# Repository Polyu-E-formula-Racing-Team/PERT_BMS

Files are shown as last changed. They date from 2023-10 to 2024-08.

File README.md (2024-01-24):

# PERT BMS Project

This project is intended to replace the previous BMS that has poor documentation and support. The first phase of this project is to build a fully functional BMS. The BMS doesn't need to be fancy, the only requirement for phase 1 is solid running.

## Timeline

| Milestone | Time |
|---|---|
| BSU HW design done | Jan 2024 |
| BSU SW design done | Feb 2024 |
| BSU stable version | Mar 2024 |
| BMU HW design done | Mar 2024 |
| BMU SW design done | Apr 2024 |
| BMU stable version | May 2024 |
| Fully function BMS | Jun 2024 |

## BMS Structure

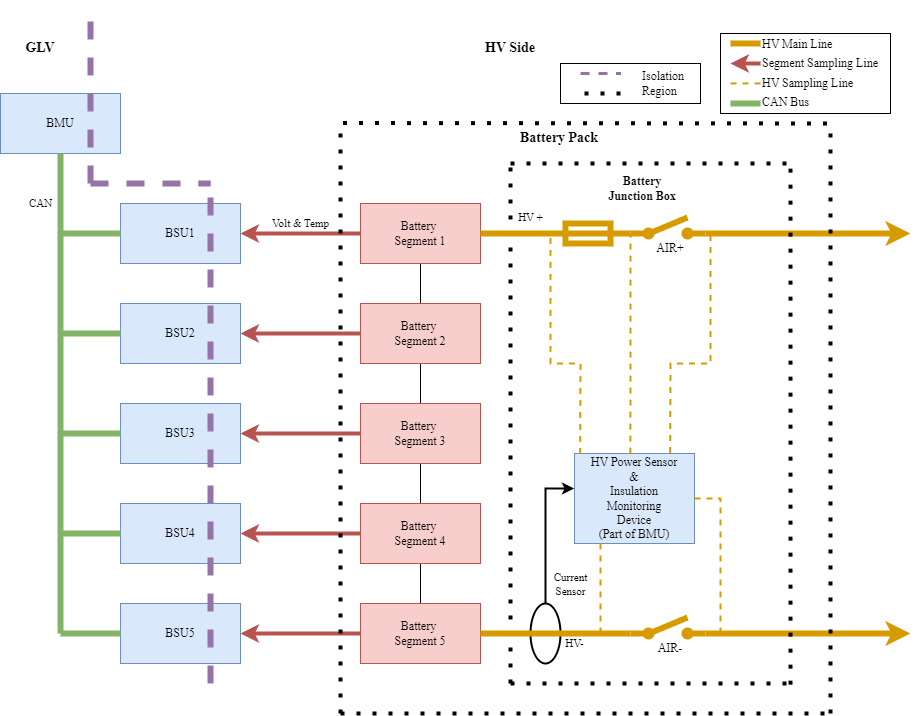
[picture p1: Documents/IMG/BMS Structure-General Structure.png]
BMS General Structure


The BMS is a distributed BMS that uses a dedicated CAN bus to share information. The core modules are 5 BSUs and 1 BMU that monitor and protect the whole accumulator.
Each BSU (Battery Sampling Unit) corresponds to one battery segment. While BMU (Battery Monitoring Unit) is monitoring the whole battery pack and coordinating the BSUs.

### BMU Structure

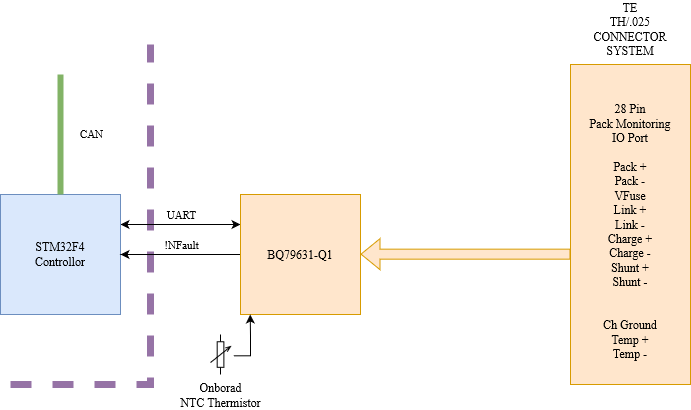
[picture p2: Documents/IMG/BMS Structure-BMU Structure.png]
BMU Structure


The BMU uses an STM32F446 MCU and a BQ76931-Q1 Battery Monitoring Chip to monitor the battery pack status. This design simplifies the design of the monitoring circuit. The core of this module is the software to estimate the SOC, SOH, DOD, etc...
The second core is the software to control cell balancing between battery packs. The third is the charging and discharge control software.

### BSU Structure

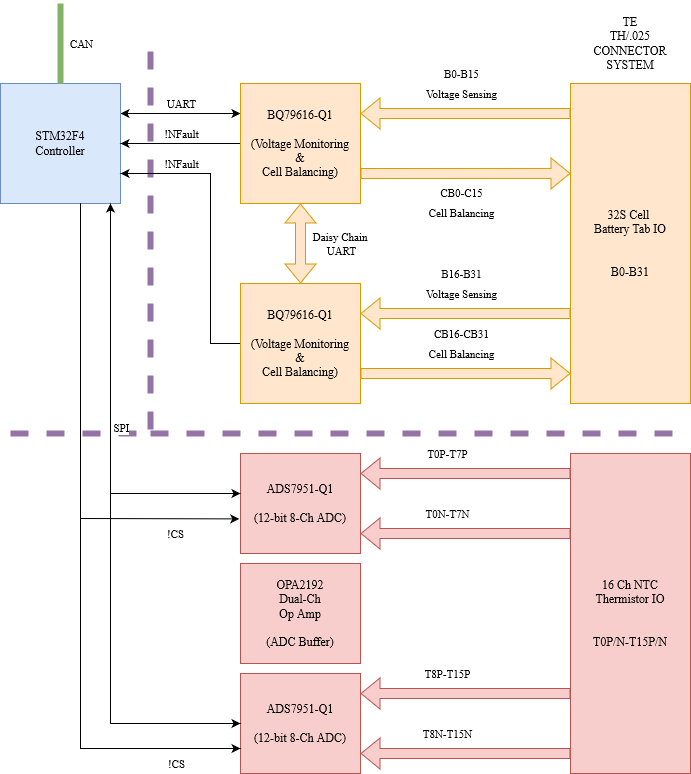
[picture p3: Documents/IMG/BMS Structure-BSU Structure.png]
BSU Structure


The BSU uses an STM32F446 MCU, two BQ79616-Q1 and two ADS7951-Q1 to sense cell property. BQ89616-Q1 measures the voltage and performs cell balancing to the battery segment.
ADS7951-Q1  sensing the temperature of the battery.
The first core of the BSU is to sample all properties and broadcast them. The second core is to control the cell balancing to quickly balance the cell voltage with the limit of 8 cells per chip.

## PCB Design

The PCBs have 4 layers of copper and use JLCPCB standard stackup. 

### BSU PCB

The BSU is 100x255 mm with 6 mounting holes. The detailed PCB design is shown in the [Description](./BSU/Documents/BSU-Description.pdf) and [Schematic](./BSU/Documents/BSU-Schematic.pdf).

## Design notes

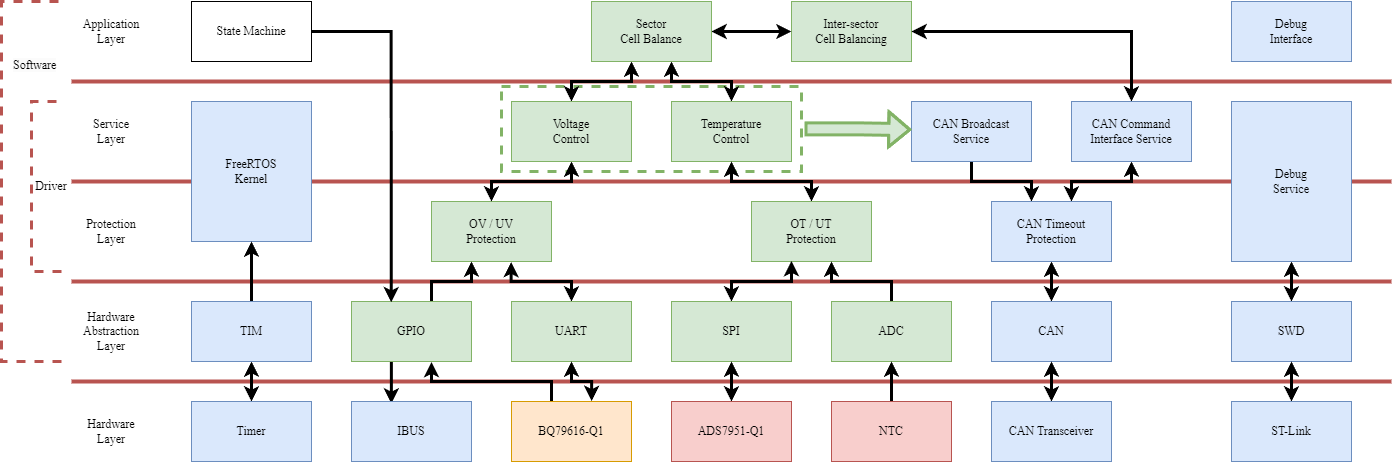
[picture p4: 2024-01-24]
Documents/IMG/BMS Structure-BSU Arch.png

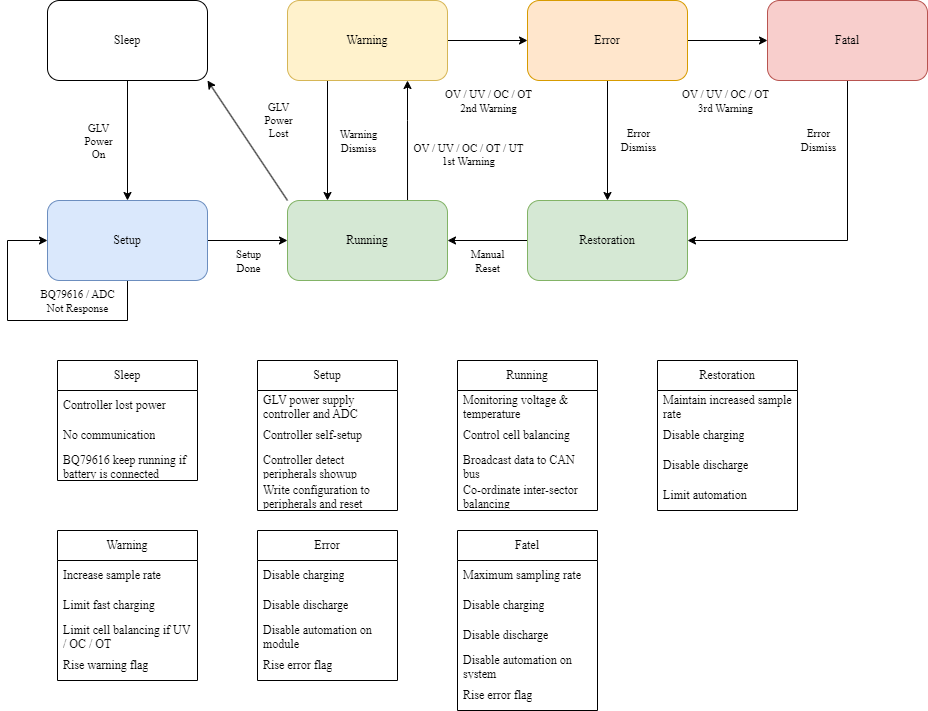
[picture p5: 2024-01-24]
Documents/IMG/BMS Structure-State Machine.png

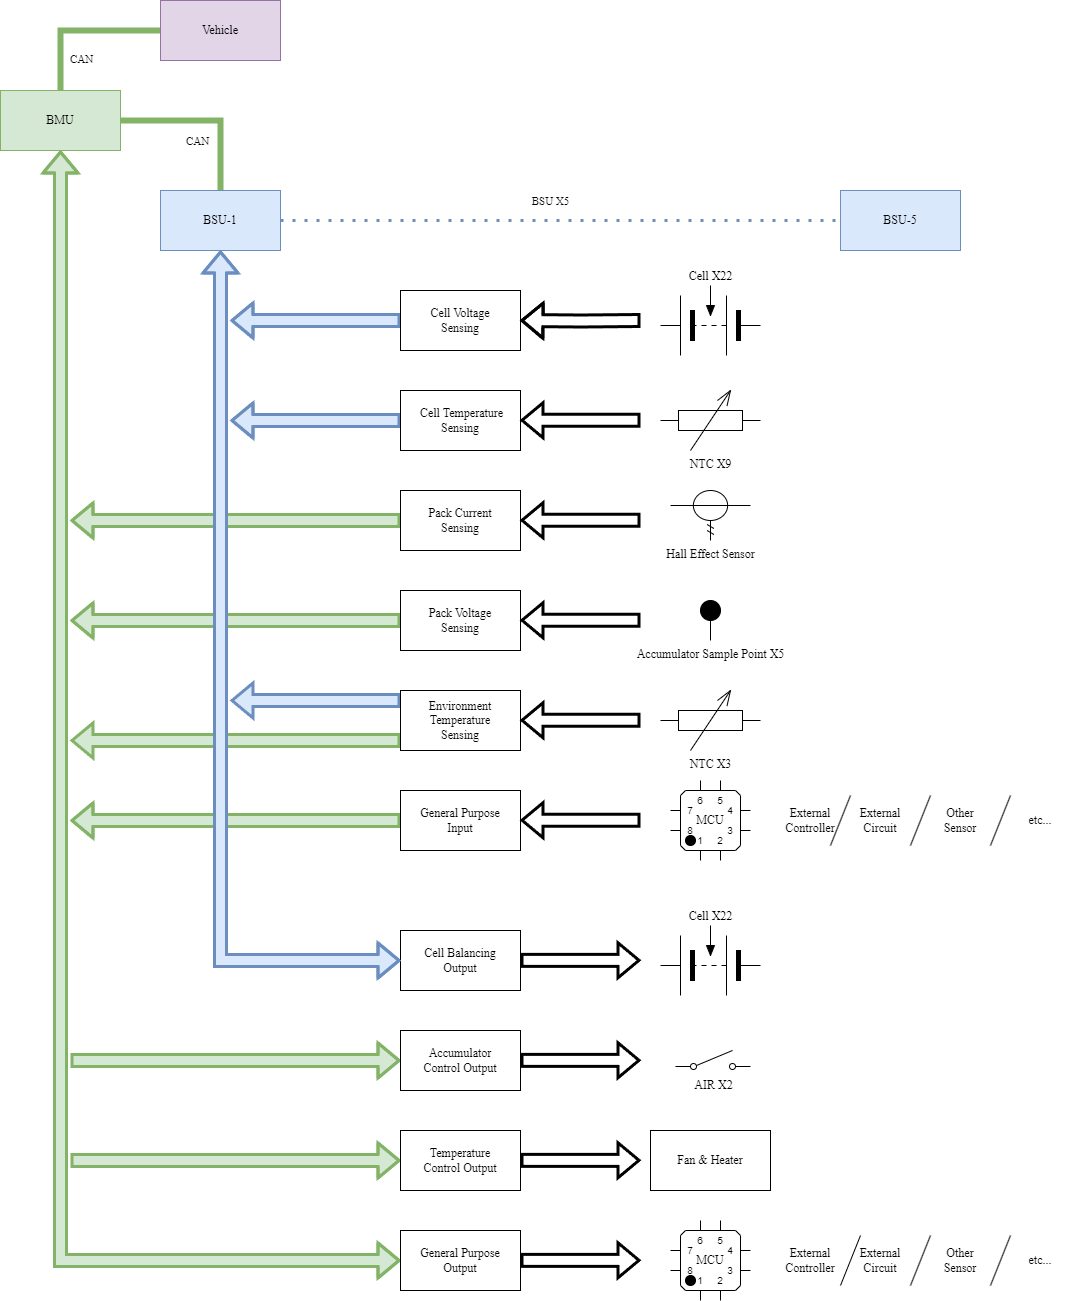
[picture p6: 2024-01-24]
Documents/IMG/BMS Structure-System IO.png

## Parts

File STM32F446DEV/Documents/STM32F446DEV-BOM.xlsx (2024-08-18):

Comment | Description | Designator | Footprint | LibRef | Quantity
NCP1117IST33T3G | Linear Voltage Regulator IC Positive Fixed 1 Output 1A SOT-223 | B1 | SOT230P700X180-4N | CMP-052-000000-1 | 1
10u | 0603 SMD Capacitor | C1, C2 | 0603_SMD_C | 0603_SMD_Capacitor | 2
100n | SMD 0603 Capacitor | C3 | 0603_SMD_RC | SMD 0603 Capacitor | 1
 | SMD 0603 Capacitor | C4, C5 | 0603_SMD_RC | SMD 0603 Capacitor | 2
Header 1x5 | Header 1x5 | J1 | HDR_1X5_2.54_SMD | Header 1x5 | 1
UJ2-MIBH-G-SMT-TR | USB Connectors USB jack, 2.0, micro B type, 5 pin, horizontal, gold flash, SMT, TR | J2 | USB_B_5P_SMD | USB_B 5P | 1
Header 1x3 | Pin Header 2.54mm Pitch STR DIP, 1x3Pin, G/F, LCP, 8.08mm*2.54mm*3.18mm, Color-Black, Bag | J3 | HDR_1X3_2.54_THD | Header 1x3 | 1
Header 1x5 | Header 2x11 | J4, J5 | HDR_2x11_2.54_THD | Header 2x11 | 2
STM32F446RET6 | No Description Available | U1 | LQFP64-STM32F446 | STM32F446RET6 | 1
ECS-1612MV-080-CN-TR | Standard Clock Oscillators 8MHz CMOS 1.6-3.6V | X1 | 1612_OSXO_80 | 8M OSXO ECS | 1
ECS-327MV-CN-TR | Standard Clock Oscillators 32.768kHz LVCMOS 1.6-3.6V | X2 | 1612_OSXO_32.768 | 32.768k OSXO ECS | 1

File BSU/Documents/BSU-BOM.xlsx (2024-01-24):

Name | Description | Designator | Footprint | Manufacturer 1 | Manufacturer_Name | Manufacturer Part Number 1 | Quantity | Supplier 1 | Supplier Currency 1 | Supplier Unit Price 1 | Supplier Subtotal 1
ADS7951QDBTRQ1 | Automotive 12 bit, 1 MSPS, 8 Channel, Single-Ended, SAR ADC | ADC1, ADC2 | TSSOP30_ADS7951 | Texas Instruments | Texas Instruments | ADS7951QDBTRQ1 | 2 | Mouser | USD | 7.42 | 14.83
BQ79616PAPR | Battery Management 16-S precision battery monitor, balancer and integrated protector with stacking interface | BQ1, BQ2 | HTQFP65_BQ79616 | Texas Instruments | Texas Instruments | BQ79616PAPRQ1 | 2 | Mouser | USD | 13.52 | 27.04
220n | 1210 SMD Capacitor | C1, C2 | 1210_SMD_C | Kyocera AVX |  | 12101C224JAT2A | 2 | Mouser | USD | 0.3903 | 0.78059
1u | 0603 SMD Capacitor | C3, C4, C13, C14, C15, C16 | 0603_SMD_C | Yageo |  | CC0603ZRY5V6BB105 | 6 | Mouser | USD | 0.03403 | 0.34026
2.2u | 0603 SMD Capacitor | C5, C6 | 0603_SMD_C | Samsung |  | CL10A225KP8NNWC | 2 | Mouser | USD | 0.10008 | 0.20015
0.1u | 0603 SMD Capacitor | C7, C8, C11, C12 | 0603_SMD_C | Yageo |  | CC0603KRX7R6BB104 | 4 | Mouser | USD | 0.04003 | 0.4003
4.7u | 0603 SMD Capacitor | C9, C10 | 0603_SMD_C | Samsung |  | CL10A475KP8NNWC | 2 | Mouser | USD | 0.10008 | 0.20015
22u | 0805 SMD Capacitor | C17, C40 | 0805_SMD_C | Murata |  | GRM21BR61C226ME44K | 2 | Mouser | USD | 0.29022 | 0.58044
1u | 0805 SMD Capacitor | C18, C20, C21, C23, C24, C33, C34, C35, C36, C37, C38, C39 | 0805_SMD_C | Samsung |  | CL21B105KBFNNNF | 12 | Mouser | USD | 0.07506 | 0.90068
10u | 0805 SMD Capacitor | C19, C22, C41, C42, C43 | 0805_SMD_C | Murata |  | GRM21BR61H106KE43L | 5 | Mouser | USD | 0.15812 | 1.58
100n | 0805 SMD Capacitor | C25, C26, C27, C28, C29, C30, C31, C32 | 0805_SMD_C | KEMET |  | C0805C104Z4VACTU | 8 | Mouser | USD | 0.04203 | 0.42032
150p | 0805 SMD Capacitor | C44, C45, C62, C63, C64 | 0805_SMD_C | KEMET |  | C0805C151J5GACTU | 5 | Mouser | USD | 0.03403 | 0.34026
150p | 0603 SMD Capacitor | C46, C47, C48, C49, C50, C51, C52, C53, C54, C55, C56, C57, C58, C59, C60, C61 | 0603_SMD_C | KEMET |  | C0603C151M5HACTU | 16 | Mouser | USD | 0.02102 | 0.33625
470n | 0603 SMD Capacitor | C65, C66, C67, C68, C69, C70, C71, C72, C73, C74, C75, C76, C77, C78, C79, C80, C81, C82, C83, C84, C85, C86, C87, C88, C89, C90, C91, C92, C93, C94, C95, C96, C97, C98, C99, C100, C101, C102, C103, C104, C105, C106, C107, C108, C109, C110, C111, C112, C113, C114, C115, C116, C117, C118, C119, C120, C121, C122, C123, C124, C125, C126, C127, C128, C129, C130 | 0603_SMD_C | Samsung |  | CL10B474KO8NFNC | 66 | Mouser | USD | 0.03102 | 2.05
470n | 0805 SMD Capacitor | C131, C132 | 0805_SMD_C | Kyocera AVX |  | 08051C474K4T2A | 2 | Mouser | USD | 0.28021 | 0.56042
10n | 0805 SMD Capacitor | C133, C134 | 0805_SMD_C | Samsung |  | CL21B103KCANNNC | 2 | Mouser | USD | 0.01901 | 0.19014
220p | 0603 SMD Capacitor | C135, C136, C141, C142 | 0603_SMD_C | Samsung |  | CL10C221JB8NFNC | 4 | Mouser | USD | 0.01801 | 0.18014
2.2n | 0603 SMD Capacitor | C137, C138, C139, C140 | 0603_SMD_C | KEMET |  | C0603C222K1RECAUTO | 4 | Mouser | USD | 0.19014 | 0.76058
824500241 | TVS Diode (Uni-directional) | D1 | SMA_824500241 | Wurth Electronics | Wurth Elektronik | 824500241 | 1 | Mouser | USD | 0.29022 | 0.29022
C1Q_1 | T&R | F1, F2, F3, F4, F5, F6, F7, F8, F9, F10, F11, F12, F13, F14, F15, F16, F17, F18, F19, F20, F21, F22, F23, F24, F25, F26, F27, F28, F29, F30, F31, F32, F33 | 1206_C1Q | Bel | Bel | C1Q1 | 33 | Mouser | USD | 0.2582 | 8.52
Header 1x2 | Header, 2-Pin | J1 | HDR_1X2_2.54_THD | Stock |  | NA | 1 | Stock | USD | 0.00128 | 0.00128
1318745-2 | TE CONNECTIVITY - 1318745-2 - Automotive Connector, TH 025 Series, Right Angle Plug, 32 Contacts, Crimp Pin | J2 | TH025_32P | Stock | TE Connectivity | NA | 1 | Stock | USD | 0.00128 | 0.00128
1318384-2 | TE Connectivity TH 025 Series, 2 Row 40 Way Through Hole Socket Automotive Header Connector, Automotive wiring | J3 | TH025_40P | Stock | TE Connectivity | NA | 1 | Stock | USD | 0.00128 | 0.00128
Header 1x3 | Pin Header 2.54mm Pitch STR DIP, 1x3Pin, G/F, LCP, 8.08mm*2.54mm*3.18mm, Color-Black, Bag | J4, J5, J10, J11, J12 | HDR_1X3_2.54_THD | Stock | Amphenol Communications Solutions | NA | 5 | Stock | USD | 0.00128 | 0.0064
Header 1x5 | Header 1x5 | J14, J15 | HDR_1X5_2.54_THD | Stock | TE Connectivity | NA | 2 | Stock | USD | 0.00128 | 0.00256
TLV75533PDBVR | LDO Voltage Regulators 500-mA, Low IQ, Small Size, Low Dropout Regulator 5-SOT-23 -40 to 125 | LDO1, LDO2 | SOT23-5_TLV75533 | Texas Instruments | Texas Instruments | TLV75533PDBVR | 2 | Mouser | USD | 0.3903 | 0.78059
RED | SMD LED | LED1, LED2, LED3, LED4, LED6 | 0805_SMD_LED | Wurth Electronics |  | 150080SS75000 | 5 | Mouser | USD | 0.19014 | 0.95072
GREEN | SMD LED | LED5 | 0805_SMD_LED | Wurth Electronics |  | 150080GS75000 | 1 | Mouser | USD | 0.19014 | 0.19014
NTCS0805E3104JXT | NTC Thermistors 100Kohms 5% SMD | NTC1, NTC2, NTC3 | 0805_SMD_R | Vishay BCcomponents | Vishay | NTCS0805E3104JXT | 3 | Mouser | USD | 0.44033 | 1.32
OPA2192IDGKT | 36-V, Precision, RRIO, Low Offset Voltage, Low Input Bias Current Op Amp With e-trim | OPA1 | VSSOP8_OPA2192 | Texas Instruments | Texas Instruments | OPA2192IDGKT | 1 | Mouser | USD | 5.44 | 5.44
VXO7805-1000 | CUI Inc.,1 A Output Current, 6~36 Vdc Input, 3 Pin SIP, Non-Isolated, Dc-Dc Converter | PS1 | VXO78xx-1000 | Stock |  | NA | 1 | Stock | USD | 0.00128 | 0.00128
PDSE1-S24-S5-M | CUI Inc., DC-DC ISOLATED, 5VDC input, 1 W, 4.5-5.5 VDC | PS2 | PDSE1-Sxx-Sx-M | Stock |  | NA | 1 | Stock | USD | 0.00128 | 0.00128
ZXTN4004KTC | Transistor | Q1, Q2, Q3, Q4 | TO252-3_ZXTN4004K | Diodes | Diodes Incorporated | ZXTN4004KTC | 4 | Mouser | USD | 0.44033 | 1.76
200 | 2010 SMD Resistor | R1, R3 | 2010_SMD_R | Bourns |  | CR2010-JW-201ELF | 2 | Mouser | USD | 0.10008 | 0.20015
100 | 2010 SMD Resistor | R2, R4 | 2010_SMD_R | Bourns |  | CR2010-JW-101ELF | 2 | Mouser | USD | 0.18014 | 0.36027
20k | 0805 SMD Resistor | R5 | 0805_SMD_R | Yageo |  | RC0805FR-0720KL | 1 | Mouser | USD | 0.10008 | 0.10008
200 | 0805 SMD Resistor | R6, R7, R8, R9, R10 | 0805_SMD_R | Yageo |  | RC0805FR-10200KL | 5 | Mouser | USD | 0.01601 | 0.16012
100 | 0805 SMD Resistor | R11, R12 | 0805_SMD_R | Yageo |  | RC0805JR-13100RL | 2 | Mouser | USD | 0.01401 | 0.14011
100k | 0603 SMD Resistor | R13, R14, R15, R16, R17, R18, R19, R20, R21, R22, R23, R24, R25, R26, R27, R28 | 0603_SMD_R | Vishay Semiconductors |  | RCA0603100KFKEA | 16 | Mouser | USD | 0.02402 | 0.38429
100k | 0805 SMD Resistor | R29, R30, R31 | 0805_SMD_R | Yageo |  | AC0805JR-07100KL | 3 | Mouser | USD | 0.01801 | 0.18014
100 | 0603 SMD Resistor | R32, R33, R34, R35, R36, R37, R38, R39, R40, R41, R42, R43, R44, R45, R46, R47, R49, R50, R51, R52, R53, R54, R55, R56, R57, R58, R59, R60, R61, R62, R63, R64, R65 | 0603_SMD_R | Yageo |  | AC0603FR-10100RL | 33 | Mouser | USD | 0.01301 | 0.42932
0 | 1210 SMD Resistor | R48 | 1210_SMD_R | Yageo |  | RC1210JR-070RL | 1 | Mouser | USD | 0.14011 | 0.14011
10 | 1210 SMD Resistor | R66, R67, R68, R69, R70, R71, R72, R73, R74, R75, R76, R77, R78, R79, R80, R81, R82, R83, R84, R85, R86, R87, R88, R89, R90, R91, R92, R93, R94, R95, R96, R97, R98 | 1210_SMD_R | KOA Speer |  | RK73B2ETTD100J | 33 | Mouser | USD | 0.05004 | 1.65
30 | 0805 SMD Resistor | R99, R100 | 0805_SMD_R | Vishay |  | CRCW080530R0FKEA | 2 | Mouser | USD | 0.10008 | 0.20015
1k | 0603 SMD Resistor | R101, R106 | 0603_SMD_R | Yageo |  | AC0603FR-101KL | 2 | Mouser | USD | 0.01301 | 0.1301
51 | 0603 SMD Resistor | R102, R103, R104, R105 | 0603_SMD_R | Yageo |  | RC0603JR-1351RL | 4 | Mouser | USD | 0.01701 | 0.17013
REF5025AIDR | 3 Vpp/V Noise, 3 ppm/C Drift Precision Series Voltage Reference | REF1 | SOIC8_REF5025 | Texas Instruments | Texas Instruments | REF5025AIDR | 1 | Mouser | USD | 3.23 | 3.23
0 | 0805 SMD Resistor | SB1, SB2, SB3, SB4 | 0805_SMD_R | Vishay Dale |  | CRCW08050000Z0EC | 4 | Mouser | USD | 0.02502 | 0.25019
ESDA041-2W3Y | Automotive dual lines 4 V TVS for BMS in SOT323 | TVS1, TVS2, TVS3, TVS4, TVS5, TVS6, TVS7, TVS8, TVS9, TVS10, TVS11, TVS12, TVS13, TVS14, TVS15, TVS16 | SOT323-3_ESDA041-2W3Y | STMicroelectronics | STMicroelectronics | ESDA041-2W3Y | 16 | Mouser | USD | 0.27921 | 4.47
SMAJ75A | LITTELFUSE - SMAJ75A - TVS Diode, SMAJ Series, Unidirectional, 75 V, 121 V, DO-214AC (SMA), 2 Pins | TVS17, TVS18 | SMA_SMAJ75A | MCC | LITTELFUSE | SMAJ75A-TP | 2 | Mouser | USD | 0.36027 | 0.72055
PESD5V0U2BT_215 | PESD5V0U2BT - Ultra low capacitance bidirectional double ESD protection diode | TVS19, TVS20, TVS21, TVS22, TVS23, TVS24, TVS25, TVS26 | SOT23-3_PESD5V0U2BT | Nexperia | Nexperia | PESD5V0U2BT,215 | 8 | Mouser | USD | 0.2582 | 2.58
ISO7741FBDW | Digital Isolators Robust EMC, quad-channel, 3/1, reinforced digital isolator 16-SOIC -55 to 125 | U3, U4, U5 | SOIC16_ISO7741 | Texas Instruments | Texas Instruments | ISO7741FBDWR | 3 | Mouser | USD | 2.93 | 8.8
TJA1050T_CM_118 | NXP - TJA1050T/CM,118 - CAN TRANSCEIVER, 1TX/RX, SOIC-8 | U6, U7 | SOIC8_TJA1050 | NXP Semiconductors | NXP | TJA1050T/CM,118 | 2 | Mouser | USD | 1.89 | 3.78
UJ2-MIBH-G-SMT-TR | USB Connectors USB jack, 2.0, micro B type, 5 pin, horizontal, gold flash, SMT, TR | USB1 | USB_B_5P_SMD | CUI Devices | CUI Devices | UJ2-MIBH-G-SMT-TR | 1 | Mouser | USD | 0.50038 | 0.50038
Littelfuse 0251.500 | Littelfuse 251 series 125VAC/125VDC 500mA | X1 | LITTELFUSE 0251 | Stock |  | NA | 1 | Stock | USD | 0.00128 | 0.00128

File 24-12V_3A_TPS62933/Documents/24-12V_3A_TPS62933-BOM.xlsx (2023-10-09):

Line # | Name | Description | Designator | Quantity | Manufacturer 1 | Manufacturer Part Number 1 | Manufacturer Lifecycle 1 | Supplier 1 | Supplier Part Number 1 | Supplier Unit Price 1 | Supplier Subtotal 1
 | TPS62933DRLR | The TPS62933 is a high-efficiency, easy-to-use synchronous buck converter with a wide input voltage range of 3.8 V to 30 V | B1 | 1 | Texas Instruments | TPS62933DRLR |  | Mouser | 595-TPS62933DRLR | 5.46 | 5.46
 | 100n | 0603 SMD Capacitor | C1 | 1 | TDK | CGA3E2X7R1E104M080AA | Volume Production | Mouser | 810-CGA3E2X7R1E104MA | 0.77938 | 0.77938
 | 47p | 0603 SMD Capacitor | C2 | 1 | TDK | C1608C0G1H470J080AA | Volume Production | Mouser | 810-C1608C0G1H470J | 0.77938 | 0.77938
 | 10u | 1206 SMD Capacitor | C3 | 1 | TDK | C3216X5R1H106K160AB | Volume Production | Mouser | 810-C3216X5R1H106K | 5.77 | 5.77
 | 100n | 0805 SMD Capacitor | C4 | 1 | KEMET | C0805C104M5RACTU | Volume Production | Mouser | 80-C0805C104M5R | 0.77938 | 0.77938
 | 33n | 0603 SMD Capacitor | C5 | 1 | Murata | GCD188R71E333KA01D | Volume Production | Mouser | 81-GCD188R71E333KA1D | 1.25 | 1.25
 | 47u | 1210 SMD Capacitor | C6 | 1 | Murata | GRM32EC81C476KE15L | Volume Production | Mouser | 81-GRM32EC81C476KE5L | 3.59 | 3.59
 | 15u | 15ÂµH Shielded Wirewound Inductor 5.03A 24.7mOhm Nonstandard | L | 1 | Eaton Cooper | DR127-150-R | Volume Production | Mouser | 704-DR127-150-R | 9.98 | 9.98
 | 68k | 0603 SMD Resistor | R1 | 1 | Vishay | CRCW060368K0FKEAHP | Volume Production | Mouser | 71-CRCW060368K0FKEAH | 1.17 | 1.17
 | 1M | 0603 SMD Resistor | R2 | 1 | Vishay Dale | RCS06031M00FKEA | Volume Production | Mouser | 71-RCS06031M00FKEA | 1.01 | 1.01
 | 330k | 0603 SMD Resistor | R3 | 1 | TE Connectivity | CRGP0603F330K | Volume Production | Mouser | 279-CRGP0603F330K | 1.01 | 1.01
 | 130k | 0603 SMD Resistor | R4 | 1 | Vishay Dale | CRCW0603130KFKEAHP | Volume Production | Mouser | 71-CRCW0603130KFKEAH | 1.09 | 1.09
 | 10k | 0603 SMD Resistor | R5, R6 | 2 | Vishay Dale | CRCW060310K0JNEAHP | Volume Production | Mouser | 71-CRCW060310K0JNEAH | 1.09 | 2.18

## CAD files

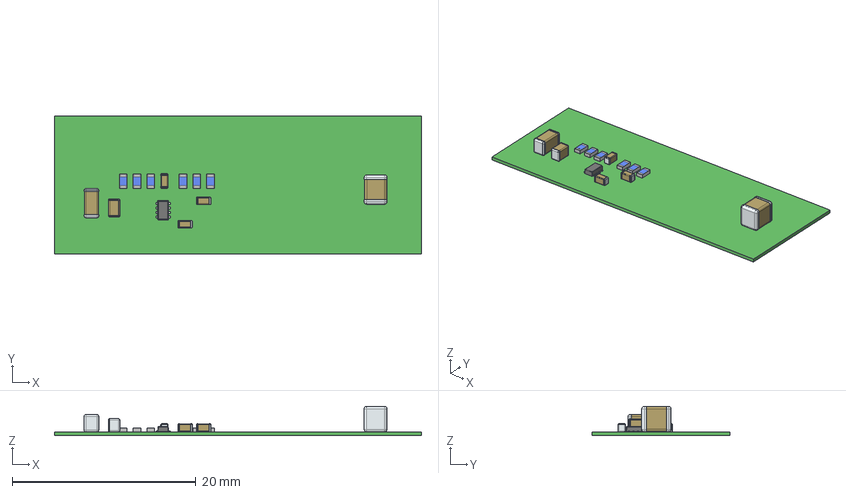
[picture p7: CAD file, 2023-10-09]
24-12V_3A_TPS62933/Documents/Converter.step
40.0 x 15.0 x 3.21 mm
0603_SMD_R x 6
BODY-SOT

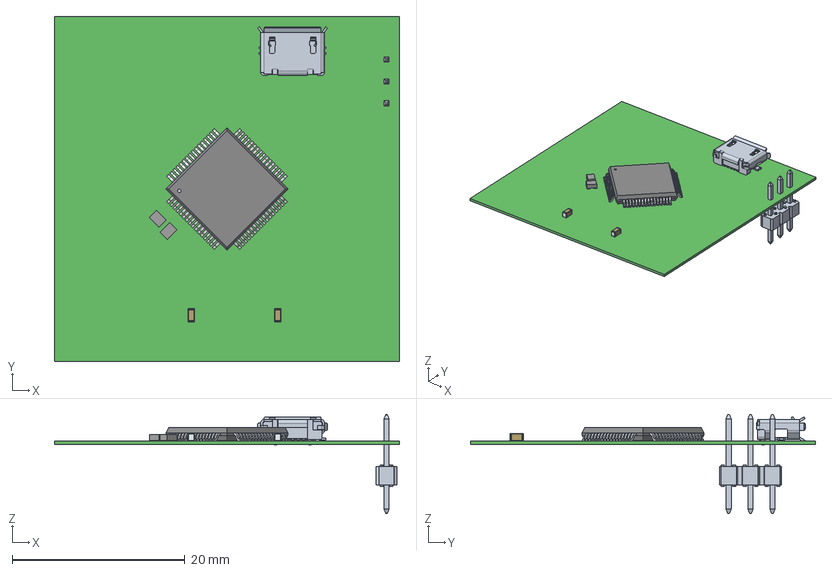
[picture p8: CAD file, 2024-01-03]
STM32F446DEV/Documents/STM32F446DEV.step
40.0 x 40.0 x 11.5 mm
Pins x 2
UJ2-MIBH-G-SMT-TR
77310_Y16 x 3

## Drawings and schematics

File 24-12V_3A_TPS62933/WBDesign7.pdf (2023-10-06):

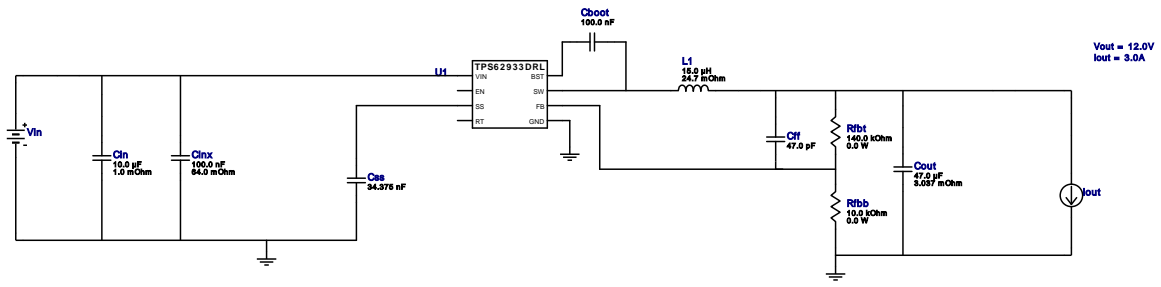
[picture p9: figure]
TPS6 2 9 3 3 DRL; VIN; GND; BST; Cinx 100.0 nF; 64.0 m Ohm; Cout 47.0 µF; 3.037 m Ohm Css 34.375 nF; L1 15.0 µH 24.7 m Ohm; Vout = 12.0V Iout = 3.0A; Rfbb 10.0 kOhm 0.0 W; Rfbt 140.0 kOhm; Cin 10.0 µF 1.0 m Ohm; Cff 47.0 pF; Cboot 100.0 nF; Iout; Vin

Copyright © 2023, Texas Instruments Incorporated | 1 | ti.com/webench

WEBENCH®
Design Report TPS62933DRLR : TPS62933DRLR 21V-29V to 12.00V @ 3A October 5, 2023 07:58:28 GMT-05:00

## WEBENCH ® Design Report

Design : 7 TPS62933DRLR
TPS62933DRLR 21V-29V to 12.00V @ 3A

VinMin = 21.0V
VinMax = 29.0V
Vout = 12.0V
Iout = 3.0A

Device = TPS62933DRLR
Topology = Buck
Created = 2023-10-04 00:13:21.644 BOM Cost = NA
BOM Count = 10
Total Pd = 1.62W

## Electrical BOM

Name | Manufacturer | Part Number | Properties | Qty Price | Footprint
Cboot | CUSTOM | CUSTOM Series= ? | Cap= 100.0 nF VDC= 10.0 V IRMS= 0.0 A
1 | NA
| | | | | CUSTOM 0 mm²
Cff | CUSTOM | CUSTOM Series= ? | Cap= 47.0 pF VDC= 24.0 V IRMS= 0.0 A
1 | NA
| | | | | CUSTOM 0 mm²
Cin | TDK | C3216X5R1H106K160AB Series= X5R | Cap= 10.0 uF ESR= 1.0 mOhm VDC= 50.0 V IRMS= 4.9 A
1 | $0.24
| | | | | 1206_180 11 mm²
Cinx | Kemet | C0805C104M5RACTU (http://capacitoredge.kemet.com/capedge2/DataSheet/Datasheet%2DC0805C104M5RACTU.pdf?pn%3DC0805C104M5RACTU) Series= X7R | Cap= 100.0 nF ESR= 64.0 mOhm VDC= 50.0 V IRMS= 1.64 A
1 | $0.01
| | | | | 0805 7 mm²
Cout | MuRata | GRM32ER61C476KE15L (http://psearch.en.murata.com/capacitor/result/smd/?status%3Dall%26pid%3DGRM32ER61C476KE15L) Series= X5R | Cap= 47.0 uF ESR= 3.037 mOhm VDC= 16.0 V IRMS= 4.59346 A
1 | $0.17
1210_280 15 mm²
Css | CUSTOM | CUSTOM Series= ? | Cap= 34.375 nF VDC= 10.0 V IRMS= 0.0 A
1 | NA
CUSTOM 0 mm²
L1 | Coiltronics | DR127-150-R (http://www.cooperbussmann.com/pdf/4a32919a%2D7470%2D4ae0%2Dbe45%2Db59e3a1351ef.pdf) | L= 15.0 µH 24.7 mOhm
1 | $0.66

DR127 210 mm²
Rfbb | CUSTOM | CUSTOM Series= ? | Res= 10.0 kOhm Power= 0.0 W Tolerance= 0.0% | 1 | NA
CUSTOM 0 mm²
Rfbt | CUSTOM | CUSTOM Series= ? | Res= 140.0 kOhm Power= 0.0 W Tolerance= 0.0% | 1 | NA
CUSTOM 0 mm²
U1 | Texas Instruments | TPS62933DRLR (http://www.ti.com/product/TPS62933) | Switcher | 1 | $0.18
DRL0008A-MFG 9 mm²

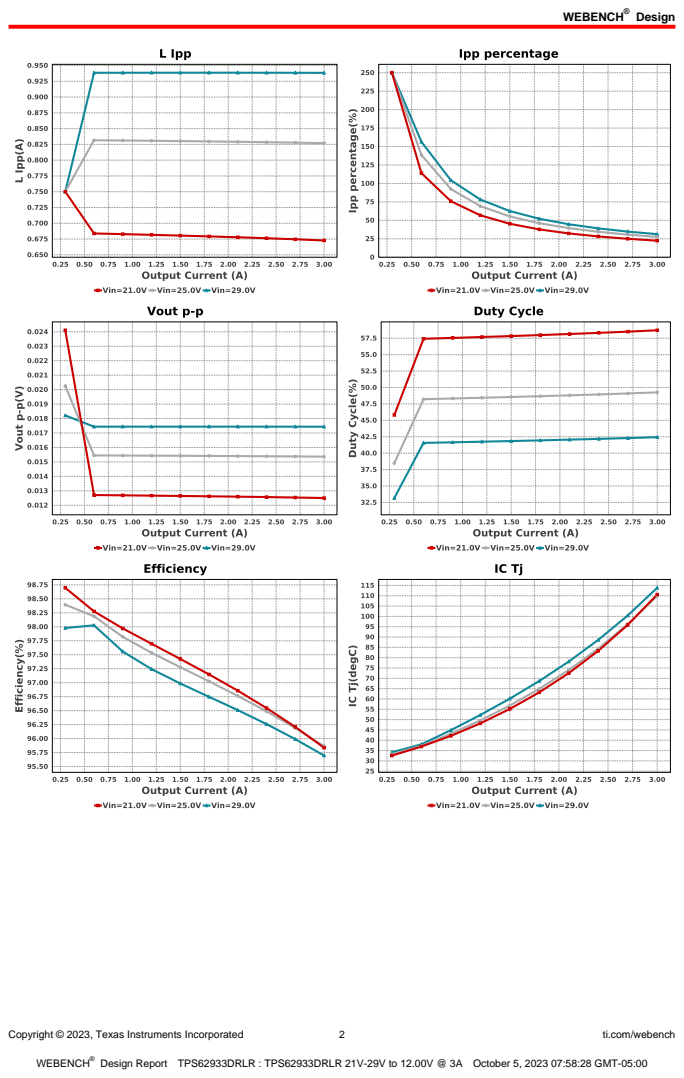
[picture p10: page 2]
Design; Copyright © 2023, Texas Instruments Incorporated; ti.com/webench

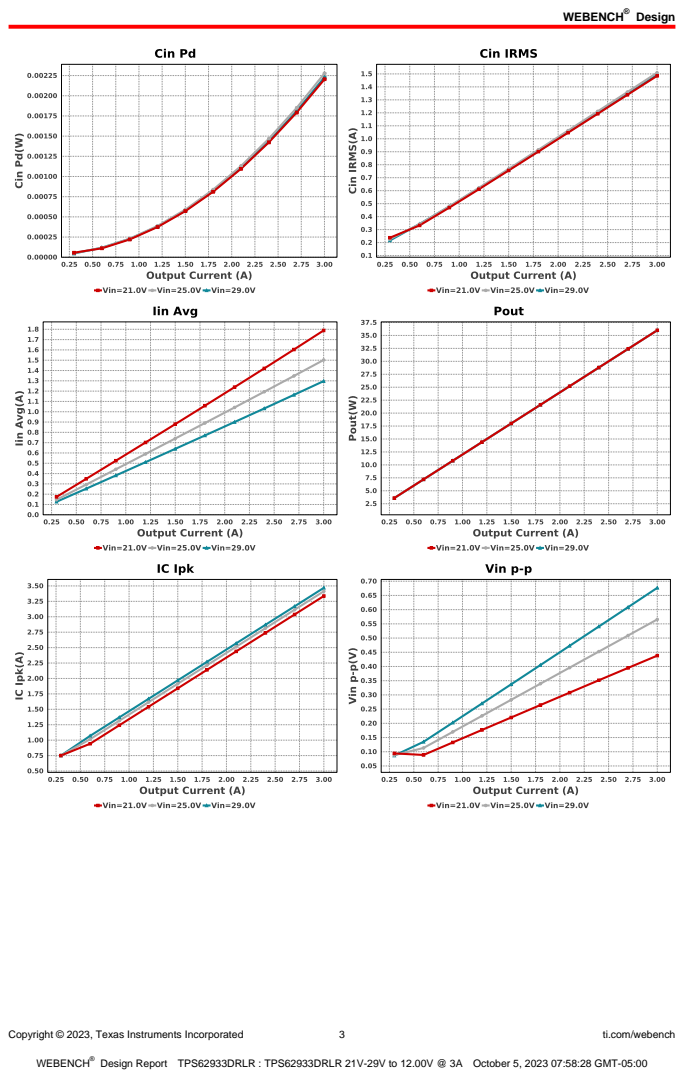
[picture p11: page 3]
Copyright © 2023, Texas Instruments Incorporated; ti.com/webench

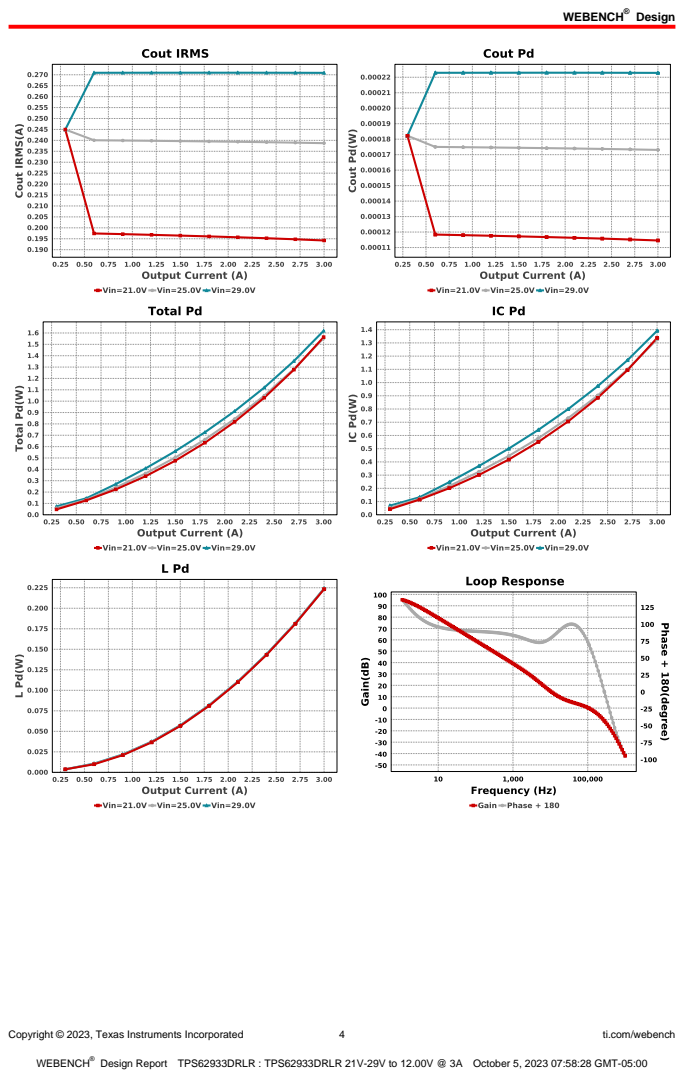
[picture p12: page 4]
Copyright © 2023, Texas Instruments Incorporated; ti.com/webench

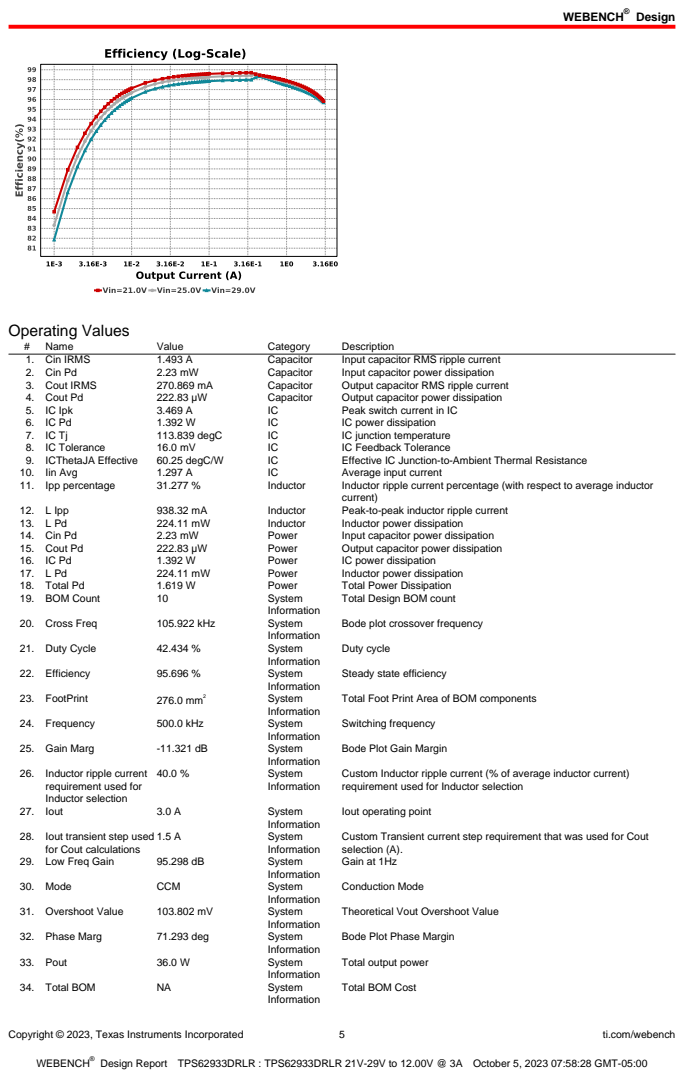
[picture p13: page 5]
Copyright © 2023, Texas Instruments Incorporated; ti.com/webench; Operating Values; Name; Value; Category; Description; 1. Cin IRMS; Capacitor; Input capacitor RMS ripple current; 2. Cin Pd; Input capacitor power dissipation; 3. Cout IRMS; Output capacitor RMS ripple current; 4. Cout Pd; Output capacitor power dissipation; 5. IC Ipk; Peak switch current in IC; IC power dissipation; 113.839 degC; IC junction temperature; 8. IC Tolerance; IC Feedback Tolerance; 9. ICThetaJA Effective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

Total Design BOM count

Bode plot crossover frequency

Steady state efficiency

Total Foot Print Area of BOM components

Bode Plot Gain Margin

26. Inductor ripple current
requirement used for
Inductor selection

Custom Inductor ripple current (% of average inductor current)
requirement used for Inductor selection

Iout operating point

28. Iout transient step used
for Cout calculations

Custom Transient current step requirement that was used for Cout
selection (A).
Gain at 1Hz

Theoretical Vout Overshoot Value

Bode Plot Phase Margin

Total output power

Total BOM Cost

Copyright © 2023, Texas Instruments Incorporated | 6 | ti.com/webench
# | Name | Value | Category | Description

35. Undershoot Value | 203.084 mV | System
| | | Information | Theoretical Vout Undershoot Value
36. Vin | 29.0 V | System
| | | Information | Vin operating point
37. Vin p-p | 676.753 mV | System
| | | Information | Peak-to-peak input voltage
38. Vout | 12.0 V | System
| | | Information | Operational Output Voltage
39. Vout Actual | 12.0 V | System
| | | Information | Vout Actual calculated based on selected voltage divider resistors
40. Vout Ripple
| requirement used for Cout calculations | 1.0 % | System Information | Custom maximum output ripple requirement that was used for Cout selection(% of Vout).
41. Vout Tolerance | 2.0 % | System
| | | Information | Vout Tolerance based on IC Tolerance (no load) and voltage divider resistors if applicable
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

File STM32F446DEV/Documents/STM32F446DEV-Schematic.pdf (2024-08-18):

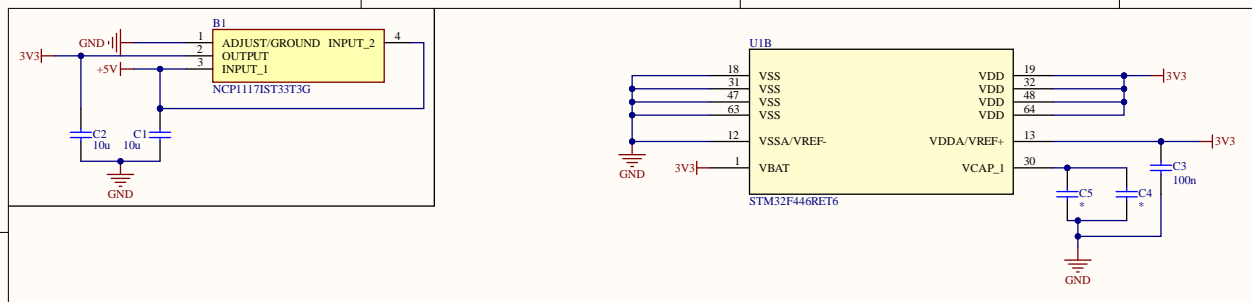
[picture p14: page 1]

B1 NCP1 O U T PU T INPU T_ 1

3 1 | 3 2
4 7 | 4 8
6 3 | | 6 4

T i tl e STM3 2F4 4 6 Devel o pmen t Board

Generat i o n N A | Organ izati o n PE RT | Su b Team E E E | Mo d u l e BMS | Ver . | Rev . A

Dat e / / | Draw n By E E E Patrick

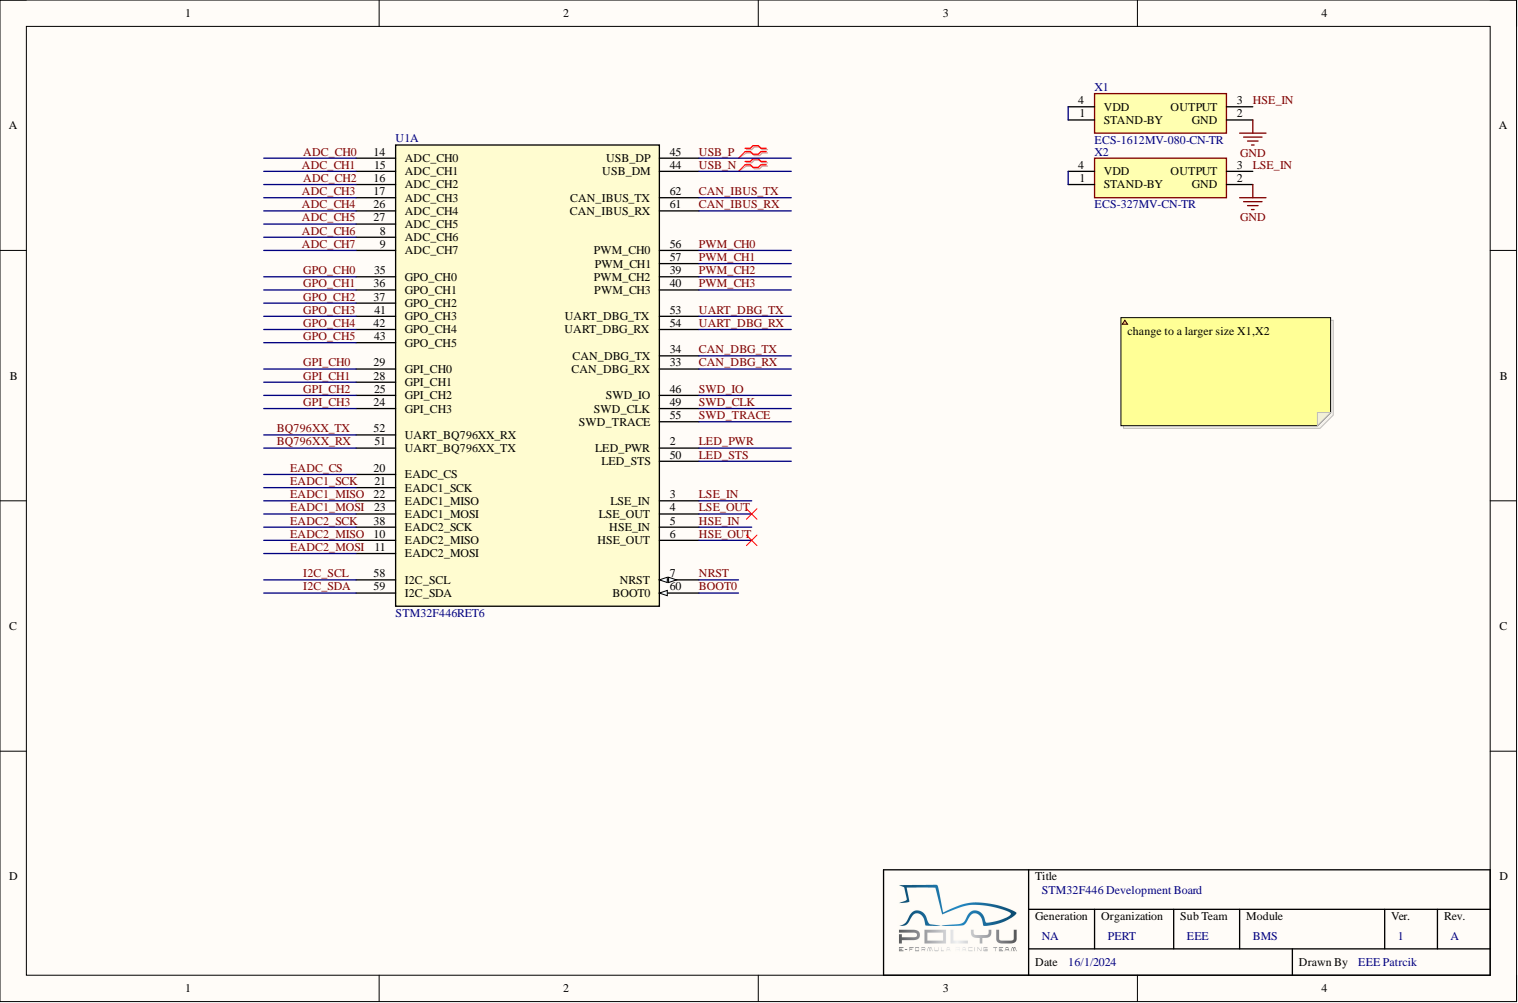
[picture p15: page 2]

T i tl e STM3 2F4 4 6 Devel o pmen t Bo ard

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

Dat e / / | Draw n By E E E Patrci k

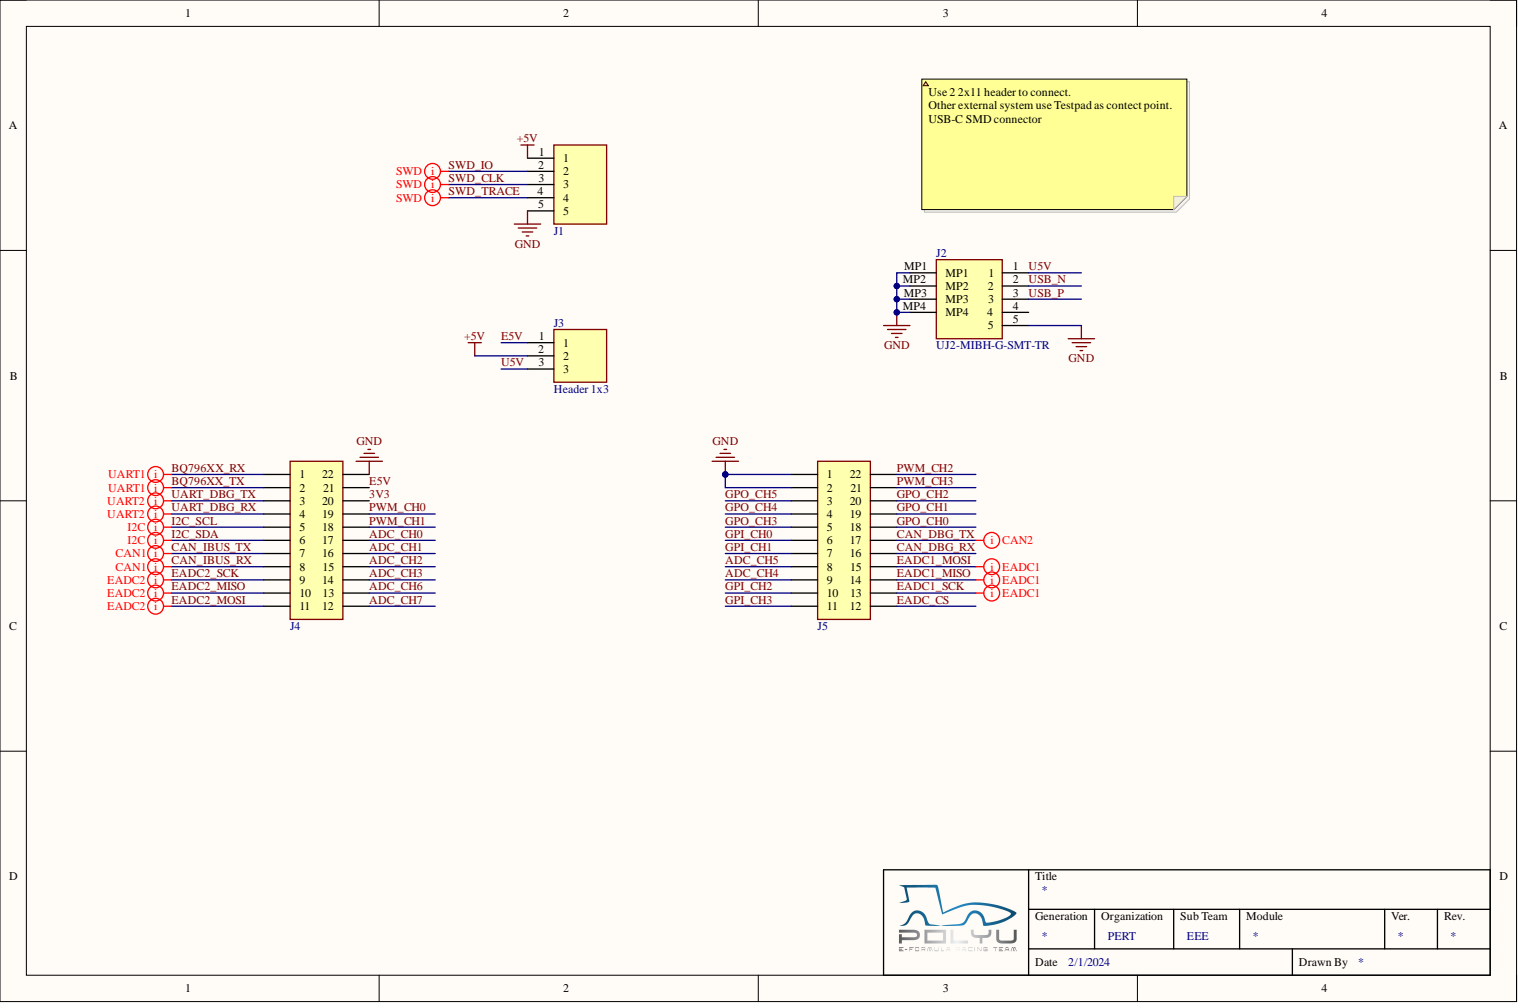
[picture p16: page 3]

Use 2 2x11 header to connect.
Other external system use Testpad as contect point.
USB-C SMD connector

Title *

Generation * | Organization PERT | Sub Team EEE | Module * | Ver. * | Rev. *

Date 2/1/2024 | Drawn By *

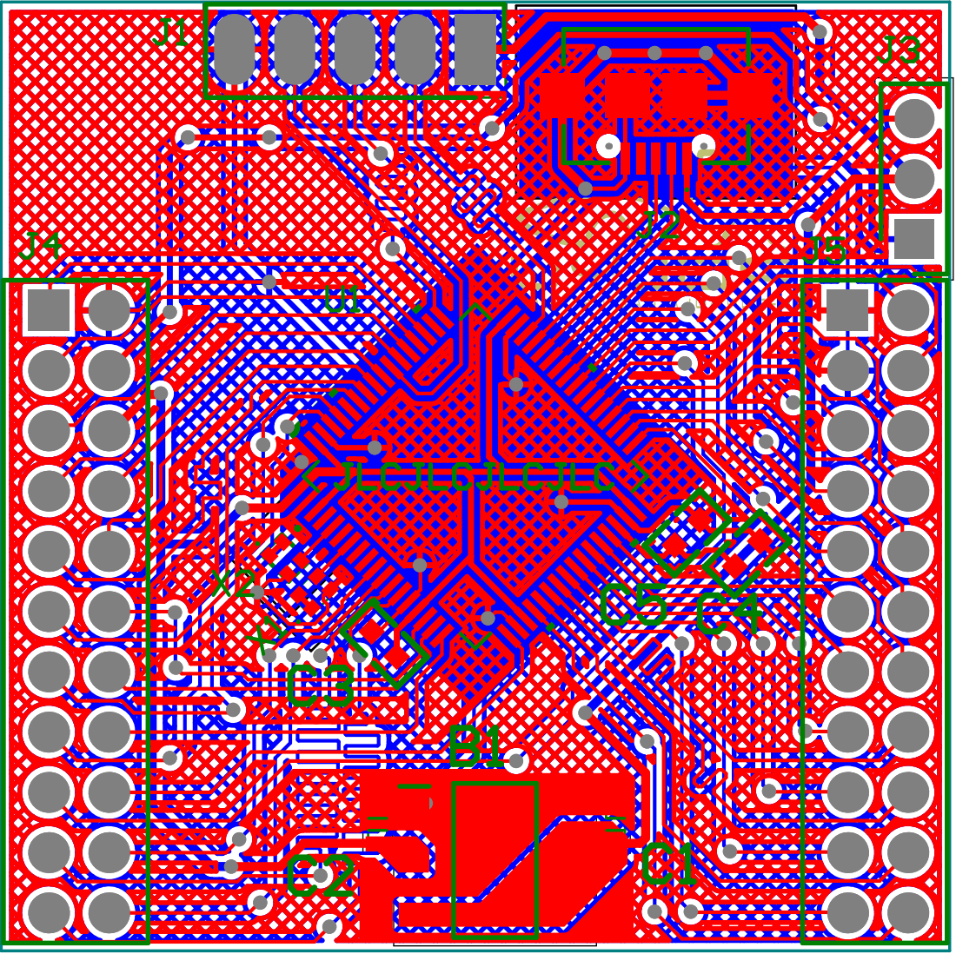
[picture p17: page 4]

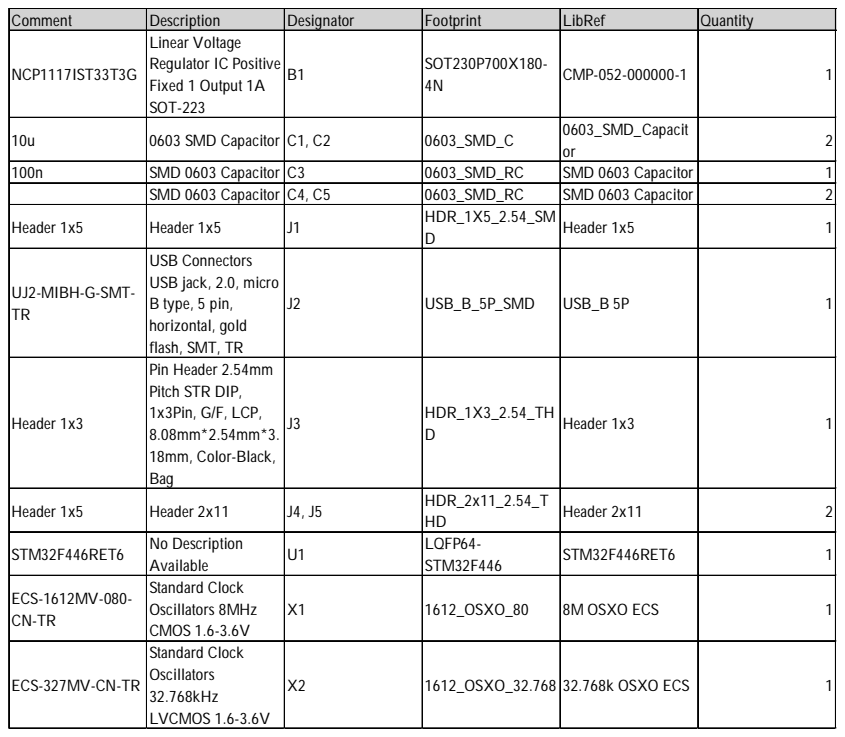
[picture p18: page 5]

Comment | Description | Designator | Footprint | LibRef | Quantity
NCP1117IST33T3G | Linear Voltage Regulator IC Positive Fixed 1 Output 1A SOT-223 | B1 | SOT230P700X180-4N | CMP-052-000000-1 | 1

10u | 0603 SMD Capacitor | C1, C2 | 0603_SMD_C | 0603_SMD_Capacit or | 2

100n | SMD 0603 Capacitor | C3 | 0603_SMD_RC | SMD 0603 Capacitor | 1

SMD 0603 Capacitor | C4, C5 | 0603_SMD_RC | SMD 0603 Capacitor | 2

Header 1x5 | Header 1x5 | J1 | HDR_1X5_2.54_SM D | Header 1x5 | 1

UJ2-MIBH-G-SMT-TR | USB Connectors USB jack, 2.0, micro B type, 5 pin, horizontal, gold flash, SMT, TR | J2 | USB_B_5P_SMD | USB_B 5P | 1

Header 1x3 | Pin Header 2.54mm Pitch STR DIP, 1x3Pin, G/F, LCP, 8.08mm*2.54mm*3. 18mm, Color-Black, Bag | J3 | HDR_1X3_2.54_TH D | Header 1x3 | 1

Header 1x5 | Header 2x11 | J4, J5 | HDR_2x11_2.54_T HD | Header 2x11 | 2

STM32F446RET6 | No Description Available | U1 | LQFP64-STM32F446 | STM32F446RET6 | 1

ECS-1612MV-080-CN-TR | Standard Clock Oscillators 8MHz CMOS 1.6-3.6V | X1 | 1612_OSXO_80 | 8M OSXO ECS | 1

ECS-327MV-CN-TR | Standard Clock Oscillators 32.768kHz LVCMOS 1.6-3.6V | X2 | 1612_OSXO_32.768 | 32.768k OSXO ECS | 1

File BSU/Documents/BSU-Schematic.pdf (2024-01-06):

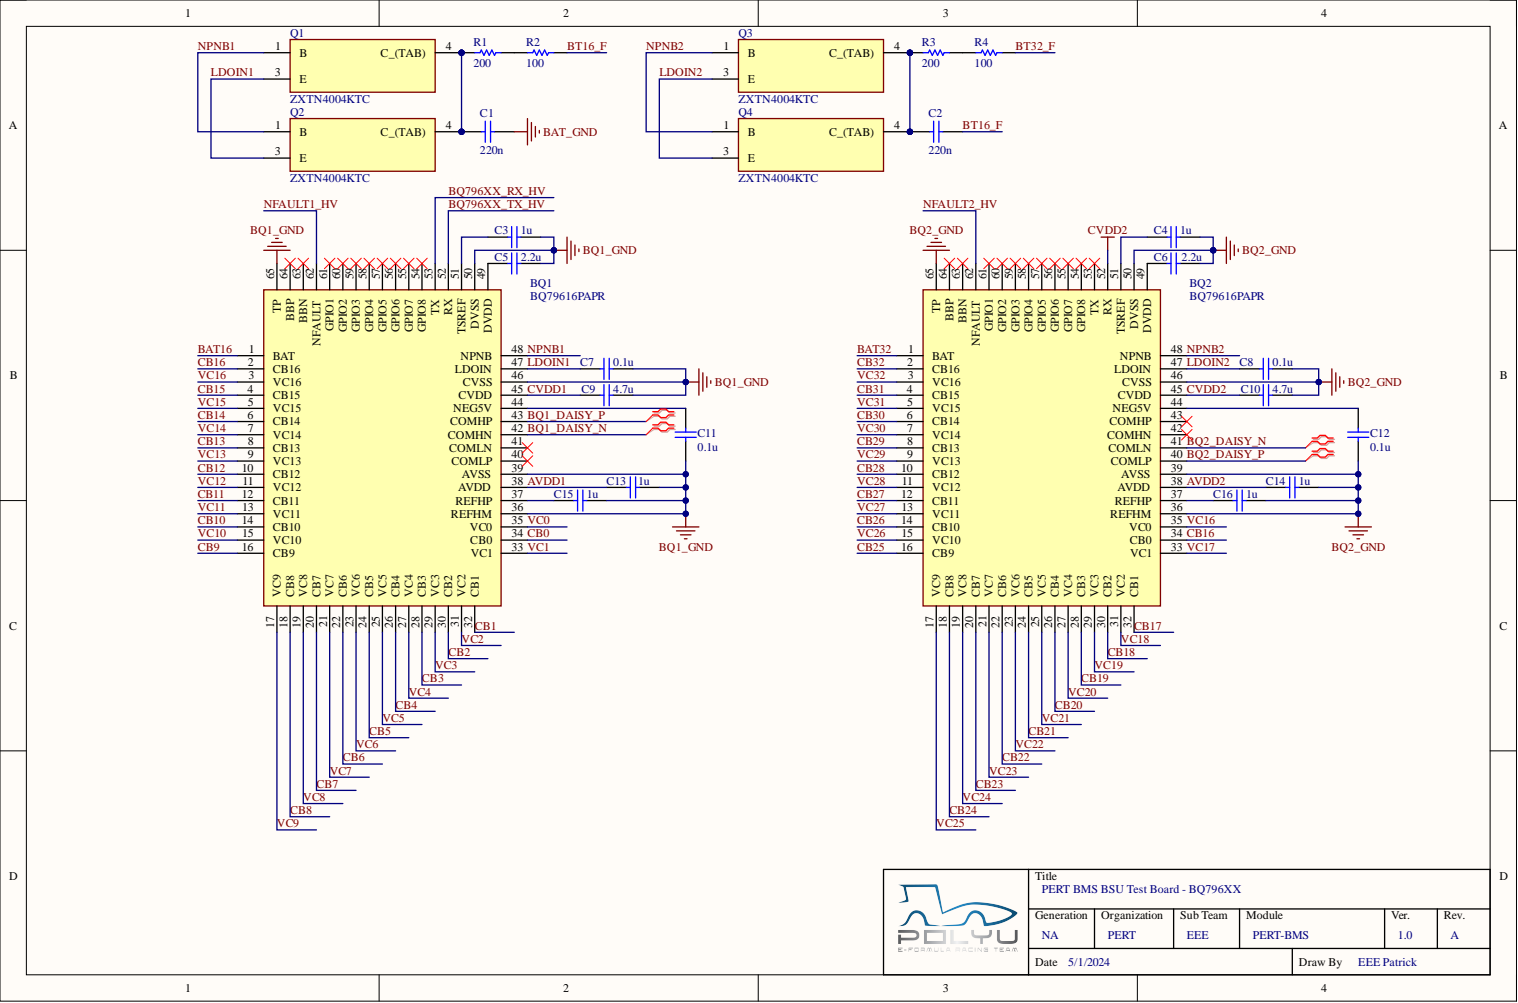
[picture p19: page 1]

Title PERT BMS BSU Test Board - BQ796XX

Generation NA | Organization PERT | Sub Team EEE | Module PERT-BMS | Ver. 1.0 | Rev. A

Date | Draw By EEE Patrick

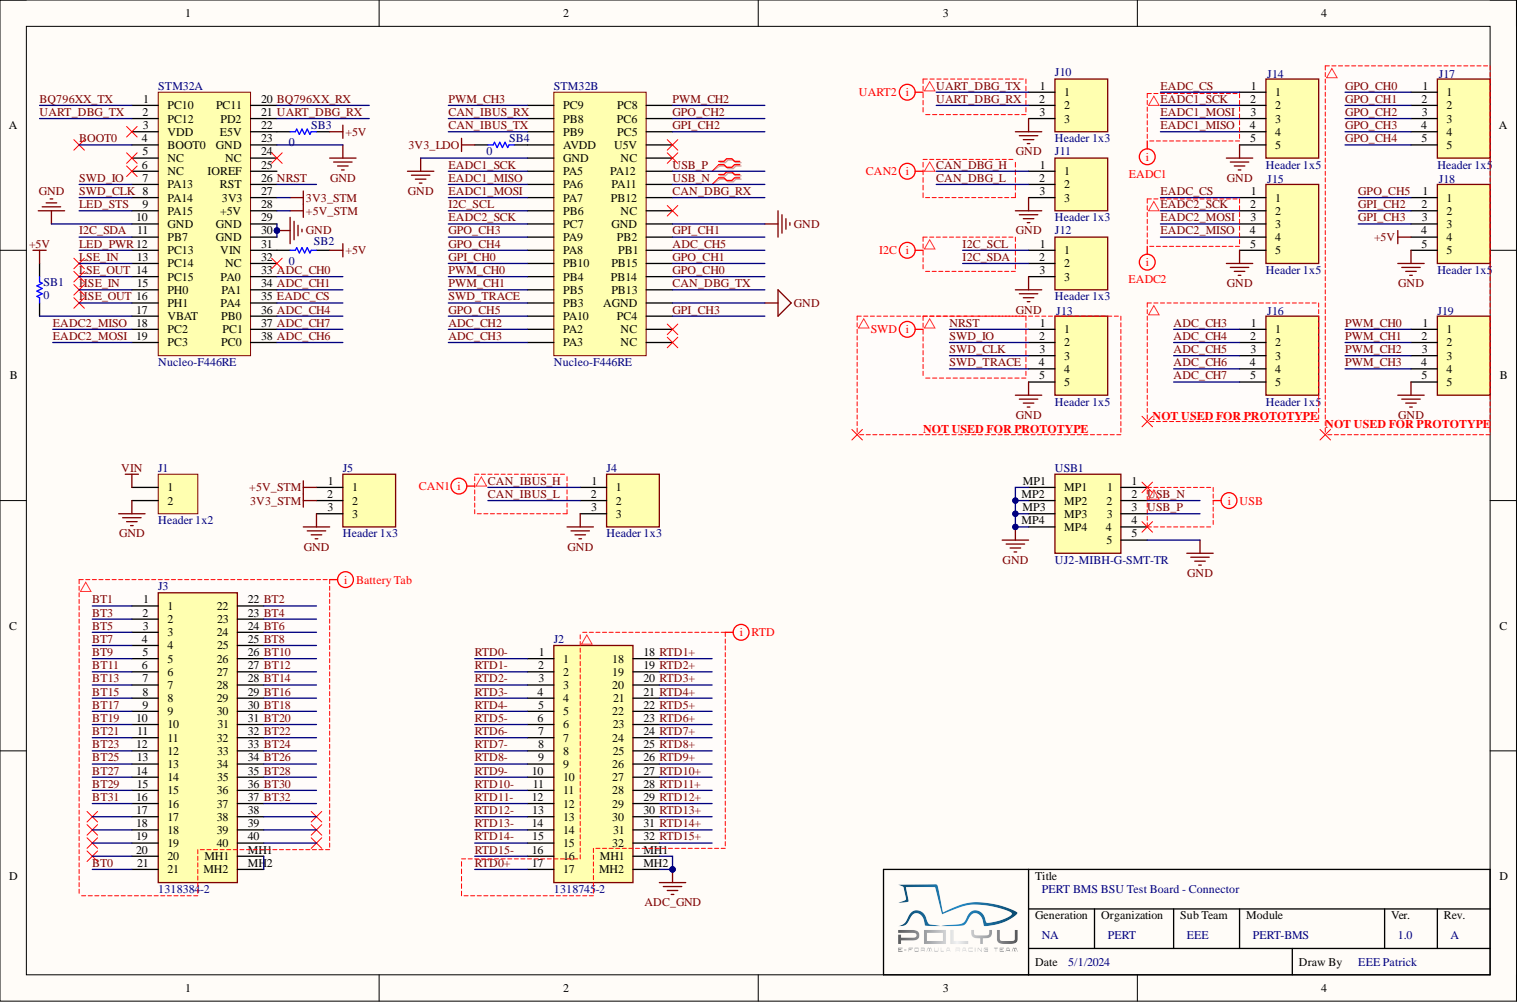
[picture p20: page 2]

T i tl e PE RT BMS BSU Tes t Board - Co n nect o r

Generat i o n N A | Organ izati o n PE RT | Su b Team E | Mo d u l e PE RT-BM S | Ver . . | Rev . A

Dat e / | Draw By E Patrick


T i tl e PE RT BMS BSU Tes t Board - Po wer

Generat i o n | Organ izati o n | Su b Team | Mo d u l e | Ver . | Rev .


Title PERT BMS BSU Test Board - Communication

Generation | Organization | Sub Team | Module | Ver. | Rev.


T i tl e PE RT BMS BSU Tes t Board - Sen s i n g

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


T i tl e PE RT BMS BSU Tes t Board -ESD

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


Title PERT BMS BSU Test Board - ADC

Generation | Organization | Sub Team | Module | Ver. | Rev.


Title PERT BMS BSU Test Board - RTD

Generation | Organization | Sub Team | Module | Ver. | Rev.


Name | Description | Designator | Footprint | Manufacturer 1 | Manufacturer_Na me | Manufacturer Part Number 1 | Quantity | Supplier 1 | Supplier Currency | Supplier Unit Price 1 | Supplier Subtotal
ADS7951QDBTRQ1 | Automotive 12 bit, 1 MSPS, 8 Channel, Single-Ended, SAR ADC | ADC1, ADC2 | TSSOP30_ADS7951 | Texas Instruments | Texas Instruments | ADS7951QDBTRQ 1 | | 2 Mouser | USD | 7.42 | 14.83
BQ79616PAPR | Battery Management 16-S precision battery monitor, balancer and integrated protector with stacking interface | BQ1, BQ2 | HTQFP65_BQ79616 | Texas Instruments | Texas Instruments | BQ79616PAPRQ1 | | 2 Mouser | USD | 13.52 | 27.04
220n | 1210 SMD Capacitor | C1, C2 | 1210_SMD_C | Kyocera AVX | | 12101C224JAT2A | | 2 Mouser | USD | 0.3903 | 0.78059
1u | 0603 SMD Capacitor | C3, C4, C13, C14, C15, C16 | 0603_SMD_C | Yageo | | CC0603ZRY5V6BB 105 | | 6 Mouser | USD | 0.03403 | 0.34026
2.2u | 0603 SMD Capacitor | C5, C6 | 0603_SMD_C | Samsung | | CL10A225KP8NN WC | | 2 Mouser | USD | 0.10008 | 0.20015
0.1u | 0603 SMD Capacitor | C7, C8, C11, C12 | 0603_SMD_C | Yageo | | CC0603KRX7R6BB 104 | | 4 Mouser | USD | 0.04003 | 0.4003
4.7u | 0603 SMD Capacitor | C9, C10 | 0603_SMD_C | Samsung | | CL10A475KP8NN WC | | 2 Mouser | USD | 0.10008 | 0.20015
22u | 0805 SMD Capacitor | C17, C40 | 0805_SMD_C | Murata | | GRM21BR61C226 ME44K | | 2 Mouser | USD | 0.29022 | 0.58044
1u | 0805 SMD Capacitor | C18, C20, C21, C23, C24, C33, C34, C35, C36, C37, C38, C39 | 0805_SMD_C | Samsung | | CL21B105KBFNNN F | 12 Mouser | | USD | 0.07506 | 0.90068
10u | 0805 SMD Capacitor | C19, C22, C41, C42, C43 | 0805_SMD_C | Murata | | GRM21BR61H106K E43L | | 5 Mouser | USD | 0.15812 | 1.58
100n | 0805 SMD Capacitor | C25, C26, C27, C28, C29, C30, C31, C32 | 0805_SMD_C | KEMET | | C0805C104Z4VAC TU | | 8 Mouser | USD | 0.04203 | 0.42032
150p | 0805 SMD Capacitor | C44, C45, C62, C63, C64 | 0805_SMD_C | KEMET | | C0805C151J5GACT U | | 5 Mouser | USD | 0.03403 | 0.34026
150p | 0603 SMD Capacitor | C46, C47, C48, C49, C50, C51, C52, C53, C54, C55, C56, C57, C58, C59, C60, C61 | 0603_SMD_C | KEMET | | C0603C151M5HAC TU | 16 Mouser | | USD | 0.02102 | 0.33625
470n | 0603 SMD Capacitor | C65, C66, C67, C68, C69, C70, C71, C72, C73, C74, C75, C76, C77, C78, C79, C80, C81, C82, C83, C84, C85, C86, C87, C88, C89, C90, C91, C92, C93, C94, C95, C96, C97, C98, C99, C100, C101, C102, C103, C104, C105, C106, C107, C108, C109, C110, C111, C112, C113, C114, C115, C116, C117, C118, C119, C120, C121, C122, C123, C124, C125, C126, C127, C128, C129, C130 | 0603_SMD_C | Samsung | | CL10B474KO8NFN C | 66 Mouser | | USD | 0.03102 | 2.05
470n | 0805 SMD Capacitor | C131, C132 | 0805_SMD_C | Kyocera AVX | | 08051C474K4T2A | | 2 Mouser | USD | 0.28021 | 0.56042
10n | 0805 SMD Capacitor | C133, C134 | 0805_SMD_C | Samsung | | CL21B103KCANN NC | | 2 Mouser | USD | 0.01901 | 0.19014
220p | 0603 SMD Capacitor | C135, C136, C141, C142 | 0603_SMD_C | Samsung | | CL10C221JB8NFN C | | 4 Mouser | USD | 0.01801 | 0.18014
2.2n | 0603 SMD Capacitor | C137, C138, C139, C140 | 0603_SMD_C | KEMET | | C0603C222K1REC AUTO | | 4 Mouser | USD | 0.19014 | 0.76058
824500241 | TVS Diode (Uni-directional) | D1 | SMA_824500241 | Wurth Electronics Wurth Elektronik | | 824500241 | | 1 Mouser | USD | 0.29022 | 0.29022
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

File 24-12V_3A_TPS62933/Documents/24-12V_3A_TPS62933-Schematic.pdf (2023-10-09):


T i tl e 2 4-1 2 V 3 A Co n verter TPS6 2 9 3 3

Generat i o n 0 6 E | Organ izati o n PE RT | Su b Team E E E | Mo d u l e Co n vert er | Ver . 1 | Rev . A

Dat e 6 / 1 0 / 2 0 2 3 | Draw n By E E E Patrick




Line # | Name | Description | Designator | Quantity | Manufacturer 1 | Manufacturer Part Number 1 | Manufacturer Lifecycle 1 | Supplier 1 | Supplier Part Number 1 | Supplier Unit Price 1 | Supplier Subtotal 1
| TPS62933DRLR | The TPS62933 is a high-efficiency, easy-to-use synchronous buck converter with a wide input voltage range of 3.8 V to 30 V | B1 | 1 Texas Instruments TPS62933DRLR | | | | Mouser | 595-TPS62933DRLR | 5.46 | 5.46
| 100n | 0603 SMD Capacitor | C1 | 1 TDK | | CGA3E2X7R1E104M080AA | Volume Production | Mouser | 810-CGA3E2X7R1E104MA | 0.77938 | 0.77938
| 47p | 0603 SMD Capacitor | C2 | 1 TDK | | C1608C0G1H470J080AA | Volume Production | Mouser | 810-C1608C0G1H470J | 0.77938 | 0.77938
| 10u | 1206 SMD Capacitor | C3 | 1 TDK | | C3216X5R1H106K160AB | Volume Production | Mouser | 810-C3216X5R1H106K | 5.77 | 5.77
| 100n | 0805 SMD Capacitor | C4 | 1 KEMET | | C0805C104M5RACTU | Volume Production | Mouser | 80-C0805C104M5R | 0.77938 | 0.77938
| 33n | 0603 SMD Capacitor | C5 | 1 Murata | | GCD188R71E333KA01D | Volume Production | Mouser | 81-GCD188R71E333KA1D | 1.25 | 1.25
| 47u | 1210 SMD Capacitor | C6 | 1 Murata | | GRM32EC81C476KE15L | Volume Production | Mouser | 81-GRM32EC81C476KE5L | 3.59 | 3.59
| 15u | 15ÂµH Shielded Wirewound Inductor 5.03A 24.7mOhm Nonstandard | L | 1 Eaton Cooper | | DR127-150-R | Volume Production | Mouser | 704-DR127-150-R | 9.98 | 9.98
| 68k | 0603 SMD Resistor | R1 | 1 Vishay | | CRCW060368K0FKEAHP | Volume Production | Mouser | 71-CRCW060368K0FKEAH | 1.17 | 1.17
| 1M | 0603 SMD Resistor | R2 | 1 Vishay Dale | | RCS06031M00FKEA | Volume Production | Mouser | 71-RCS06031M00FKEA | 1.01 | 1.01
| 330k | 0603 SMD Resistor | R3 | 1 TE Connectivity | | CRGP0603F330K | Volume Production | Mouser | 279-CRGP0603F330K | 1.01 | 1.01
| 130k | 0603 SMD Resistor | R4 | 1 Vishay Dale | | CRCW0603130KFKEAHP | Volume Production | Mouser | 71-CRCW0603130KFKEAH | 1.09 | 1.09
| 10k | 0603 SMD Resistor | R5, R6 | 2 Vishay Dale | | CRCW060310K0JNEAHP | Volume Production | Mouser | 71-CRCW060310K0JNEAH | 1.09 | 2.18

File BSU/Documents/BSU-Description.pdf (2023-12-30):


PERT BMS BSU Testing Board

Title PERT-BMS BSU TestBoard

Generation NA | Organization PERT | Sub Team EEE | Module PERT-BMS | Ver. 1.0 | Rev.

Date | Drawn By EEE Patrick


Title
PERT-BMS BSU TestBoard


Title PERT-BMS BSU TestBoard

Generation | Organization | Sub Team | Module | Ver. | Rev.


Assembly View from Top side (Scale 1:1)


Assembly View from Bottom side (Scale 1:1)

Title
PERT-BMS BSU TestBoard


Via Type Type 2B (Scale 16:1)

Title PERT-BMS BSU TestBoard

Generation | Organization | Sub Team | Module | Ver. | Rev.


Title
PERT-BMS BSU TestBoard


Drill Drawing View (Scale 1:1)

Title
PERT-BMS BSU TestBoard


Title
PERT-BMS BSU TestBoard


Bill Of Materials (Top)

C44, C45, C62, C63, C64 | 150p | 5
C46, C47, C48, C49, C50, C51, C52, C53, C54, C55, C56, C57, C58, C59, C60, C61 | 150p | 16

R99, R100 | 30 | | 2
REF1 | REF5025AIDR | REF5025AIDR | 1

SB1, SB2, SB3, SB4 | 0 | | 4
TVS1, TVS2, TVS3, TVS4, TVS5, TVS6, TVS7, TVS8, TVS9, TVS10, TVS11, TVS12, TVS13, TVS14, TVS15, TVS16 | ESDA041-2W3Y | ESDA041-2W3Y | 16

C131, C132 | 470n | | 2
C133, C134 | 10n | | 2
D1 | 824500241 | 824500241 | 1

TVS19, TVS20, TVS21, TVS22, TVS23, TVS24, TVS25, TVS26 | PESD5V0U2BT_215 | PESD5V0U2BT,215 | 8

J1 | Header 1x2 | 1

LDO1, LDO2 | TLV75533PDBVR | TLV75533PDBVR | 2
LED1, LED2, LED3, LED4, LED6 | RED | | 5

Title PERT-BMS BSU TestBoard

LED5 | GREEN | | 1
NTC1, NTC2 | NTCS0805E3104JXT | NTCS0805E3104JXT | 2
OPA1 | OPA2192IDGKT | OPA2192IDGKT | 1

Generation | Organization | Sub Team | Module | Ver. | Rev.


Bill Of Materials (Bottom)

Designator | Name | Manufacturer_Part_Nu mber | Quantity

C135, C136, C141, C142 | 220p | | 4
C137, C138, C139, C140 | 2.2n | | 4
F1, F3, F5, F7, F9, F11, F13, F15, F17, F19, F21, F23, F25, F27, F29, F31, F33 | C1Q_1 | C1Q 1 | 17

NTC3 | NTCS0805E3104JXT | NTCS0805E3104JXT | 1

R101, R106 | 1k | | 2
R102, R103, R104, R105 | 51 | | 4

Title PERT-BMS BSU TestBoard

Generation | Organization | Sub Team | Module | Ver. | Rev.


The PCB should always have a bottom cover rigidly mounted that made by Insulation
material that have minimun 3mm thick and comply at least UL94 V-0, i.e. PC ,FR4 or
Normex.

The PCB most apply at least 2 layers of Conformal Coating before used. Each layer of
coating must sit and wait for minimum of 24 hours till it's dry out. Mask all the
connector before apply the coating.

Title PERT-BMS BSU TestBoard

Generation | Organization | Sub Team | Module | Ver. | Rev.

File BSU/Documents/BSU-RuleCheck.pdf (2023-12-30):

### Electrical Rules Check Report

Class | Document | Message
Warning | BSU_Connector.SchDoc | Floating Power Object +5V at (10700mil,5800mil)
Warning | BSU_Connector.SchDoc | Floating Power Object GND at (7800mil,4700mil)
Warning | BSU_Connector.SchDoc | Floating Power Object GND at (10700mil,4700mil)
Warning | BSU_Connector.SchDoc | Floating Power Object GND at (10700mil,5700mil)
Warning | BSU_Power.SchDoc | Net 24V has no driving source (Pin C19-2, Pin C21-2, Pin D1-1, Pin PS1-1, Pin PS2-2, Pin
| | R5-2, Pin X1-2)
Warning | BSU_Comm.SchDoc | Nets Wire RTD0- has multiple names (Net Label RTD0- (2), Net Label RTD1- (2), Net
| | Label RTD2- (2), Net Label RTD3- (2), Net Label RTD4- (2), Net Label RTD5- (2), Net
| | Label RTD6- (2), Net Label RTD7- (2), Net Label RTD8- (2), Net Label RTD9- (2), Net
| | Label RTD10- (2), Net Label RTD11- (2), Net Label RTD12- (2), Net Label RTD13- (2),
| | Net Label RTD14- (2), Net Label RTD15- (2), Power Object ADC_GND (18))
30 | 2023 10:33:40 PM | Page 1 of 1

### Design Rules Verification Report

Filename : D:\EE\BMS\BSU\BSU.PcbDoc | Warnings 0

### Rule Violations 96

Warnings
Total | 0
30 | 2023 10:33:44 PM | Page 1 of 5



Silk To Solder Mask (Clearance=0.15mm) (IsPad),(All)
Silk To Solder Mask Clearance Constraint: (0.127mm < 0.15mm) Between Pad F10-1(211.2mm,22.505mm) on Top Cu And Track (211.2mm,23.392mm)(211.2mm,24.408mm) on Top Overlay [Top Overlay] to [Top Solder
Silk To Solder Mask Clearance Constraint: (0.127mm < 0.15mm) Between Pad F10-2(211.2mm,25.295mm) on Top Cu And Track (211.2mm,23.392mm)(211.2mm,24.408mm) on Top Overlay [Top Overlay] to [Top Solder
Silk To Solder Mask Clearance Constraint: (0.127mm < 0.15mm) Between Pad F1-1(221.1mm,22.505mm) on Bottom Cu And Track (221.1mm,23.392mm)(221.1mm,24.408mm) on Bottom Overlay [Bottom Overlay] to [Bottom
Silk To Solder Mask Clearance Constraint: (0.127mm < 0.15mm) Between Pad F11-1(210.1mm,22.505mm) on Bottom Cu And Track (210.1mm,23.392mm)(210.1mm,24.408mm) on Bottom Overlay [Bottom Overlay] to [Bottom
Silk To Solder Mask Clearance Constraint: (0.127mm < 0.15mm) Between Pad F11-2(210.1mm,25.295mm) on Bottom Cu And Track (210.1mm,23.392mm)(210.1mm,24.408mm) on Bottom Overlay [Bottom Overlay] to [Bottom
Silk To Solder Mask Clearance Constraint: (0.127mm < 0.15mm) Between Pad F1-2(221.1mm,25.295mm) on Bottom Cu And Track (221.1mm,23.392mm)(221.1mm,24.408mm) on Bottom Overlay [Bottom Overlay] to [Bottom
Silk To Solder Mask Clearance Constraint: (0.127mm < 0.15mm) Between Pad F12-1(209mm,22.505mm) on Top Cu And Track (209mm,23.392mm)(209mm,24.408mm) on Top Overlay [Top Overlay] to [Top Solder] clearance
Silk To Solder Mask Clearance Constraint: (0.127mm < 0.15mm) Between Pad F12-2(209mm,25.295mm) on Top Cu And Track (209mm,23.392mm)(209mm,24.408mm) on Top Overlay [Top Overlay] to [Top Solder] clearance
Silk To Solder Mask Clearance Constraint: (0.127mm < 0.15mm) Between Pad F13-1(207.9mm,22.505mm) on Bottom Cu And Track (207.9mm,23.392mm)(207.9mm,24.408mm) on Bottom Overlay [Bottom Overlay] to [Bottom
Silk To Solder Mask Clearance Constraint: (0.127mm < 0.15mm) Between Pad F13-2(207.9mm,25.295mm) on Bottom Cu And Track (207.9mm,23.392mm)(207.9mm,24.408mm) on Bottom Overlay [Bottom Overlay] to [Bottom
Silk To Solder Mask Clearance Constraint: (0.127mm < 0.15mm) Between Pad F14-1(206.8mm,22.505mm) on Top Cu And Track (206.8mm,23.392mm)(206.8mm,24.408mm) on Top Overlay [Top Overlay] to [Top Solder
Silk To Solder Mask Clearance Constraint: (0.127mm < 0.15mm) Between Pad F14-2(206.8mm,25.295mm) on Top Cu And Track (206.8mm,23.392mm)(206.8mm,24.408mm) on Top Overlay [Top Overlay] to [Top Solder
Silk To Solder Mask Clearance Constraint: (0.127mm < 0.15mm) Between Pad F15-1(205.7mm,22.505mm) on Bottom Cu And Track (205.7mm,23.392mm)(205.7mm,24.408mm) on Bottom Overlay [Bottom Overlay] to [Bottom
Silk To Solder Mask Clearance Constraint: (0.127mm < 0.15mm) Between Pad F15-2(205.7mm,25.295mm) on Bottom Cu And Track (205.7mm,23.392mm)(205.7mm,24.408mm) on Bottom Overlay [Bottom Overlay] to [Bottom
Silk To Solder Mask Clearance Constraint: (0.127mm < 0.15mm) Between Pad F16-1(204.6mm,22.505mm) on Top Cu And Track (204.6mm,23.392mm)(204.6mm,24.408mm) on Top Overlay [Top Overlay] to [Top Solder
Silk To Solder Mask Clearance Constraint: (0.127mm < 0.15mm) Between Pad F16-2(204.6mm,25.295mm) on Top Cu And Track (204.6mm,23.392mm)(204.6mm,24.408mm) on Top Overlay [Top Overlay] to [Top Solder
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

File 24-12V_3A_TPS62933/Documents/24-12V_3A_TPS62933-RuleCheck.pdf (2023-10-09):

### Electrical Rules Check Report

Class | Document | Message Successful Compile for 24-12V_3A_TPS62933.PrjPcb
9 | 2023 6:47:38 PM | Page 1 of 1


Design Rules Verification Report

SMD Neck-Down Constraint (Percent=95%) (All)
SMD Neck-Down Constraint: Between Pad C6-2(35mm,8.45mm) on Top Layer And Track (34.1mm,8.45mm)(35mm,8.45mm) on Top Layer Relative Track Width: 112.06%

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

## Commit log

2023-10-06 Create BMS_ShareComponentLibrary
2023-10-06 design complete
    [24-12V_3A_TPS62933-BOM.xlsx, 24-12V_3A_TPS62933.PrjPcb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]
2023-10-08 Update BMS_ShareComponentLibrary
2023-10-09 update feedback path
    [24-12V_3A_TPS62933-BOM.xlsx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]
2023-12-27 Remove Unused GPIO from BSU
    [BSU_Connector.SchDoc]
2024-01-06 updated SCH template and draftsman template and regenerate all files
    [BSU-BOM.xlsx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]
2024-01-24 Update
    Fixed Gerber generation
    Created simple Doc based on FYP
    [BSU-BOM.xlsx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]
2024-04-05 Added Battery Simulator to sim a battery pack with Power supply
    [BAT_Simulator.GBL, BAT_Simulator.GBO, BAT_Simulator.GBP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]
2024-08-18 some update
    [MCU.SchDoc, Power.SchDoc, STM32F446DEV-BOM.csv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]

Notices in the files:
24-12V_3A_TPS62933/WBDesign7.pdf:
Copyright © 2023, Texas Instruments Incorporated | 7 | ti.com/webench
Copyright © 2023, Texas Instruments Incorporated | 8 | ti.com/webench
